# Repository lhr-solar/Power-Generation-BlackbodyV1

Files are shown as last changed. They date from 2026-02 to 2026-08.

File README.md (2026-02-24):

# Power Generation Blackbody
Gathers irradiance and temperature data for telemetry and MPPT algorithmic input.

**Blackbody**

Gathers irradiance reading from sensor board and temperature reading from thermocouple. Sends data on telemetry CAN bus.

**Irradiance Sensor Board**

Holds the irradiance sensor. Placed on the top shell between solar modules and connected with wires to blackbody

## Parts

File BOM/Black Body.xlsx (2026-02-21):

Reference | Qty | Value | DNP | Exclude from BOM | Exclude from Board | Footprint | Datasheet | P/N
Alert_1,Alert_2 | 2 | LED |  |  |  | LED_SMD:LED_0603_1608Metric_Pad1.05x0.95mm_HandSolder | ~ | LS Q976.01-N1Q2-1
C2 | 1 | 1uF |  |  |  | Capacitor_SMD:C_0805_2012Metric_Pad1.18x1.45mm_HandSolder | ~ | MLASU168SB5105KTNA01
C3 | 1 | 0.1u |  |  |  | Capacitor_SMD:C_0805_2012Metric_Pad1.18x1.45mm_HandSolder | ~ | MLASH168SB7104KTNA01
F2 | 1 | 0.5 |  |  |  | Fuse:Fuseholder_Blade_Mini_Keystone_3568 | ~ | 3557-2
FB1,FB2 | 2 | 200 |  |  |  | Inductor_SMD:L_0603_1608Metric_Pad1.05x0.95mm_HandSolder | ~ | 742792910
GND1,Irrad_Fuse1,TP_TC_1,TP_TC_2,TP_TC_F_1,TP_TC_F_2,VCC1 | 7 | TestPoint |  |  |  | TestPoint:TestPoint_Keystone_5005-5009_Compact | ~ | 5015
IC2 | 1 | MCP96L00T-E_MX |  |  |  | BlackBody:QFN65P500X500X100-21N-D | https://datasheet.datasheetarchive.com/originals/distributors/DKDS41/DSANUWW0026539.pdf | MCP96L00T-E/MX
J1 | 1 | 53307-2471 |  |  |  | utsvt_connectors:PeripheralSOM | https://www.molex.com/en-us/products/part-detail-pdf/533072471?display=pdf | 53307-2471
J2 | 1 | Conn_01x02 |  |  |  | utsvt_connectors:105313-2102 | ~ | C17189968
J4 | 1 | LogicAnalyzer |  |  |  | utsvt_connectors:CONN_SFH11-xxxC-D05-ST-XX_SUL | https://www.digikey.com/en/products/detail/sullins-connector-solutions/SFH11-PBPC-D05-ST-BK/1990087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 | SFH11-PBPC-D05-ST-BK
J5 | 1 | Conn_02x04_Top_Bottom |  |  |  | Connector_Molex:Molex_Nano-Fit_105314-xx08_2x04_P2.50mm_Horizontal | ~ | C841208
J7 | 1 | Conn_02x03_Top_Bottom |  |  |  | utsvt_connectors:105314-1306 | ~ | C493437
LOGO1 | 1 | Dr. Hallock |  |  |  | utsvt_logos:LHRs_LOGO
LOGO2 | 1 | Dr. Hallock |  |  |  | utsvt_logos:Hallock_Image_Tiny
R1,R2,R3,R11,R15,R16 | 6 | 10k |  |  |  | Resistor_SMD:R_0603_1608Metric_Pad0.98x0.95mm_HandSolder | ~ | CRCW060310K0FKEI ,CRCW06031K00FKEI ,CRCW080510K0FKEA
R4 | 1 | 1M |  |  |  | Resistor_SMD:R_0603_1608Metric_Pad0.98x0.95mm_HandSolder | ~ | 0603WAF1004T5E
R5,R6 | 2 | 100 |  |  |  | Resistor_SMD:R_0603_1608Metric_Pad0.98x0.95mm_HandSolder | ~ | CRCW0603100RFKEA
R7,R8 | 2 | 2M |  |  |  | Resistor_SMD:R_0603_1608Metric_Pad0.98x0.95mm_HandSolder | ~ | 0603WAF2004T5E
R9 | 1 | 0 |  |  |  | Resistor_SMD:R_0603_1608Metric_Pad0.98x0.95mm_HandSolder | ~ | CRCW06030000Z0EE
R12 | 1 | 43k |  |  |  | Resistor_SMD:R_0603_1608Metric_Pad0.98x0.95mm_HandSolder | ~ | CRCW060343K0FKEI
R13,R14 | 2 | 1k |  |  |  | Resistor_SMD:R_0603_1608Metric_Pad0.98x0.95mm_HandSolder | ~ | CRCW08051K50FKEA

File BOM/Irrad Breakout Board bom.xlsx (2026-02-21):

Quantity | LCSC Part # | "Description" (Customer #)
1 | MLASU168SB5105KTNA01 | Capacitor 0805 1 µF X7R 50 V (Customer: CAP_0805_1uF_X7R)
1 | 105313-1105 | Molex Nano-Fit header, right-angle, 1×5, 2.50 mm (Customer: NANOFIT_RA_1x5)
1 | CRCW080510K0FKEA | Resistor 0805 10 kΩ ±1% (Customer: RES_0805_10K_1PCT)
2 | CRCW08051K50FKEA | Resistor 0805 1.5 kΩ ±1% (Customer: RES_0805_1K5_1PCT)
1 | TSL25911FN | TSL25911FN ambient light sensor, FN package (Customer: TSL25911FN_ALS)

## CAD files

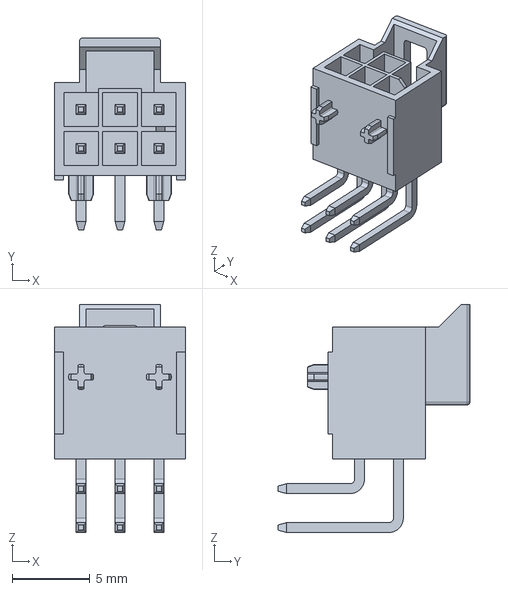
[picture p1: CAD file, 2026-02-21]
Hardware/Blackbody/3D Models/Molex Nanofit 2x3 Connector.stp
8.44 x 12.3 x 14.7 mm

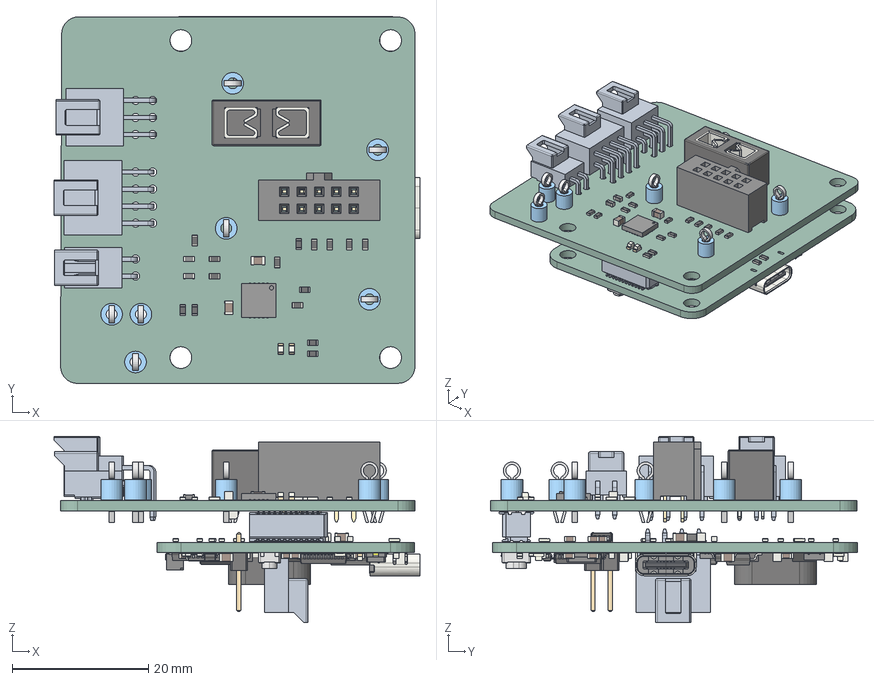
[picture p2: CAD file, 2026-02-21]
Hardware/Blackbody/Black Body.step
53.6 x 53.8 x 27.3 mm
LED_0603_1608Metric x 11
R_0603_1608Metric x 46
ThermalPin x 2
PinsArrayLR x 4
PinsArrayTB x 2
TestPoint_Keystone_5005-5009_Compact x 7
C_0805_2012Metric x 14
SFH11-xC-Dx-ST-BK body_05
pin^SFH11-xC-Dx-ST-BK Ass x 10
L_0603_1608Metric x 2
Fuseholder_Blade_Mini_Keystone_3568
C_0603_1608Metric x 25
D_SOD-123F x 2
LQFP-48_7x7mm_P0.5mm
SOT-223
kicad_embedded_DC8F7DF302591227B9F71E251B6FE682
kicad_embedded_70E7614803E5E4F918B4D78DA69A18BB
L_Coilcraft_MSS1246-XXX
USB_C_Receptacle_GCT_USB4105-xx-A_16P_TopMnt_Horizontal
kicad_embedded_9406EA57197DC5EF7108E35EAA086FA7
BODY-SO x 2
LEAD-D0008A x 8
TL3365AF180QG--3DModel-STEP-520916
BODY-TSSOP
LEAD-TSSOP x 16
PIN1
DAP
SOT-143
D_SOD-123
PinHeader_1x02_P2.54mm_Vertical
D_SOD-323
SOT-23W
LEAD-SO x 8
PeripheralSOM_PCB
Black Body_PCB

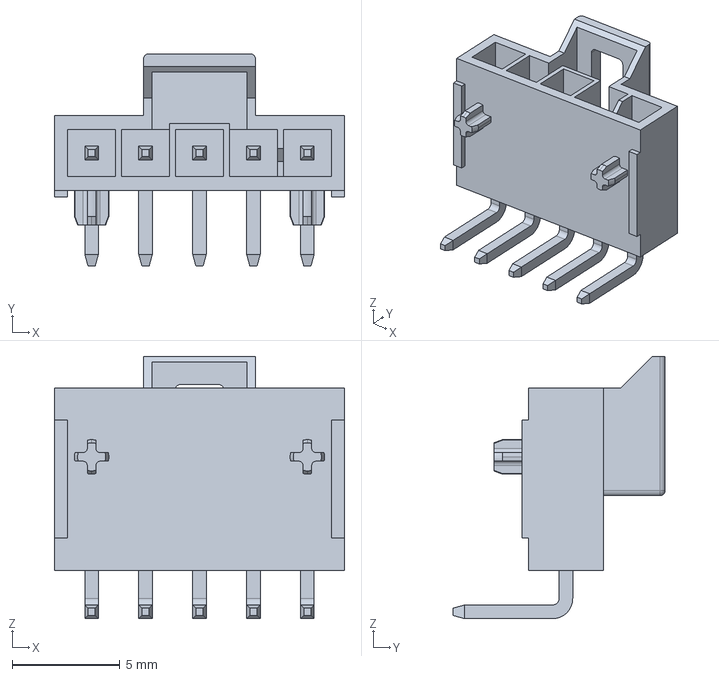
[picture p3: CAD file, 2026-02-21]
Hardware/IrradianceBreakout/3D Models/Molex Nanofit 1x5 Connector.stp
13.4 x 9.84 x 12.2 mm

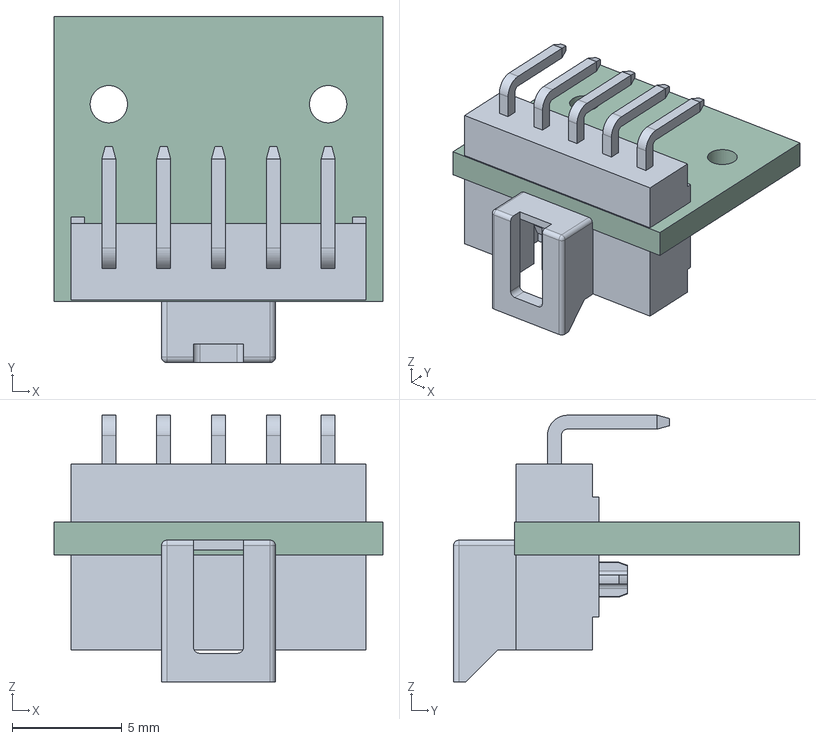
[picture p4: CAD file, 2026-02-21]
Hardware/IrradianceBreakout/Black Body Breakout Board.step
15.0 x 15.8 x 12.2 mm
Black Body Breakout Board_PCB

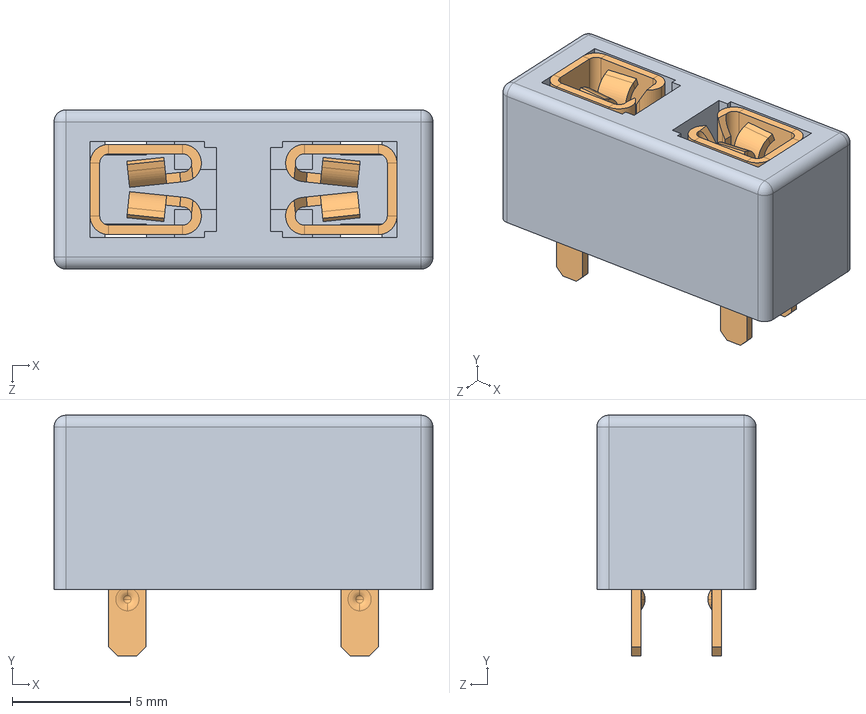
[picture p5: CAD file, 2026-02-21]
Hardware/Blackbody/3D Models/Fuse 3658.STEP
16.0 x 10.2 x 6.73 mm
F3568-1
3557_rev.C x 2

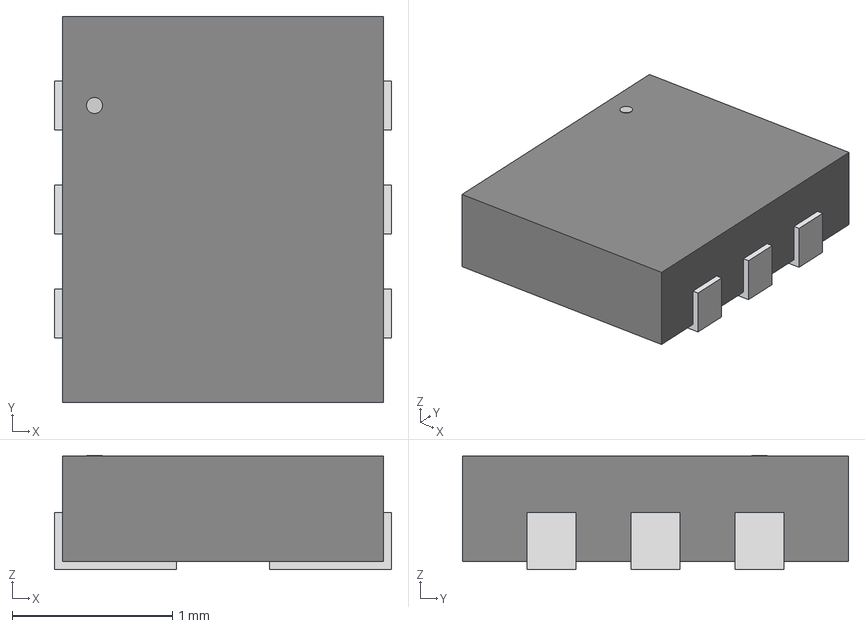
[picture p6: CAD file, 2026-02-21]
Hardware/IrradianceBreakout/3D Models/Irrad IC.step
2.11 x 2.41 x 0.714 mm

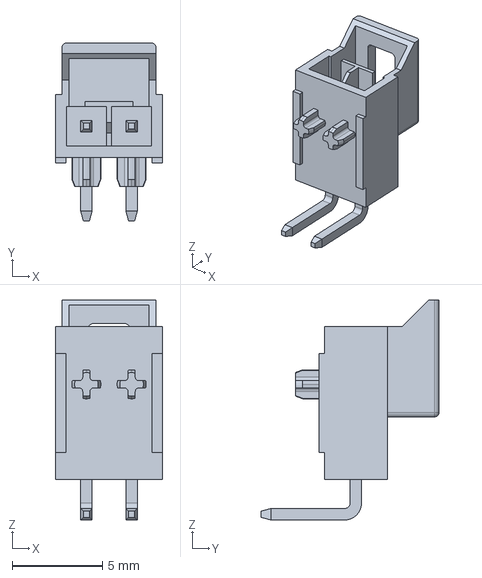
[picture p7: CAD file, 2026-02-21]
Hardware/Blackbody/3D Models/Molex Nanofit 1x2 Connector.stp
5.94 x 9.84 x 12.2 mm

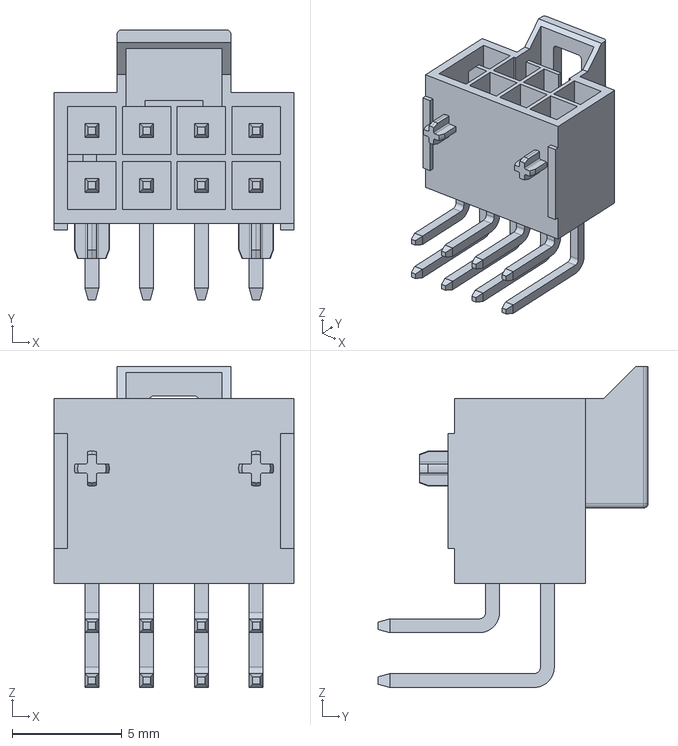
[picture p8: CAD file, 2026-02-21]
Hardware/Blackbody/3D Models/Molex Nanofit 2x4 Connector.stp
10.9 x 12.3 x 14.7 mm

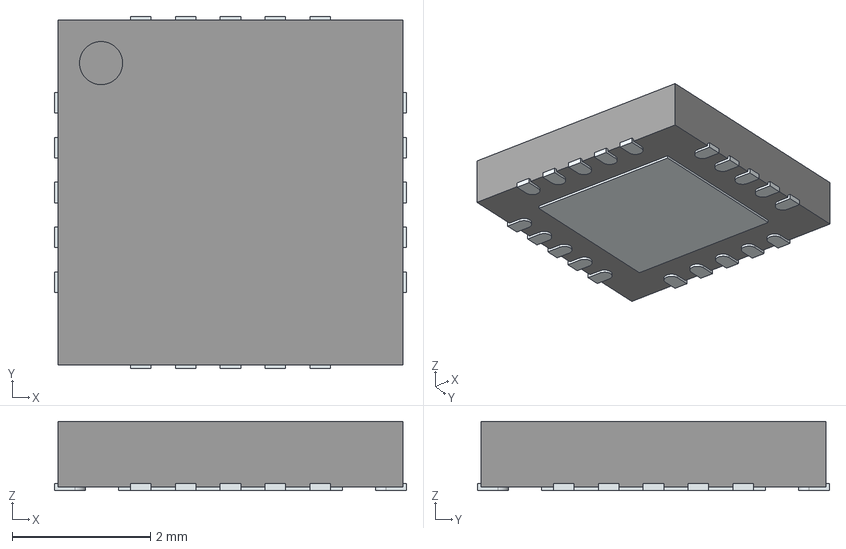
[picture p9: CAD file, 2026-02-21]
Hardware/Blackbody/3D Models/MCP96L00T-E_MX.stp
5.10 x 5.10 x 1.00 mm
ThermalPin
PinsArrayLR
PinsArrayTB

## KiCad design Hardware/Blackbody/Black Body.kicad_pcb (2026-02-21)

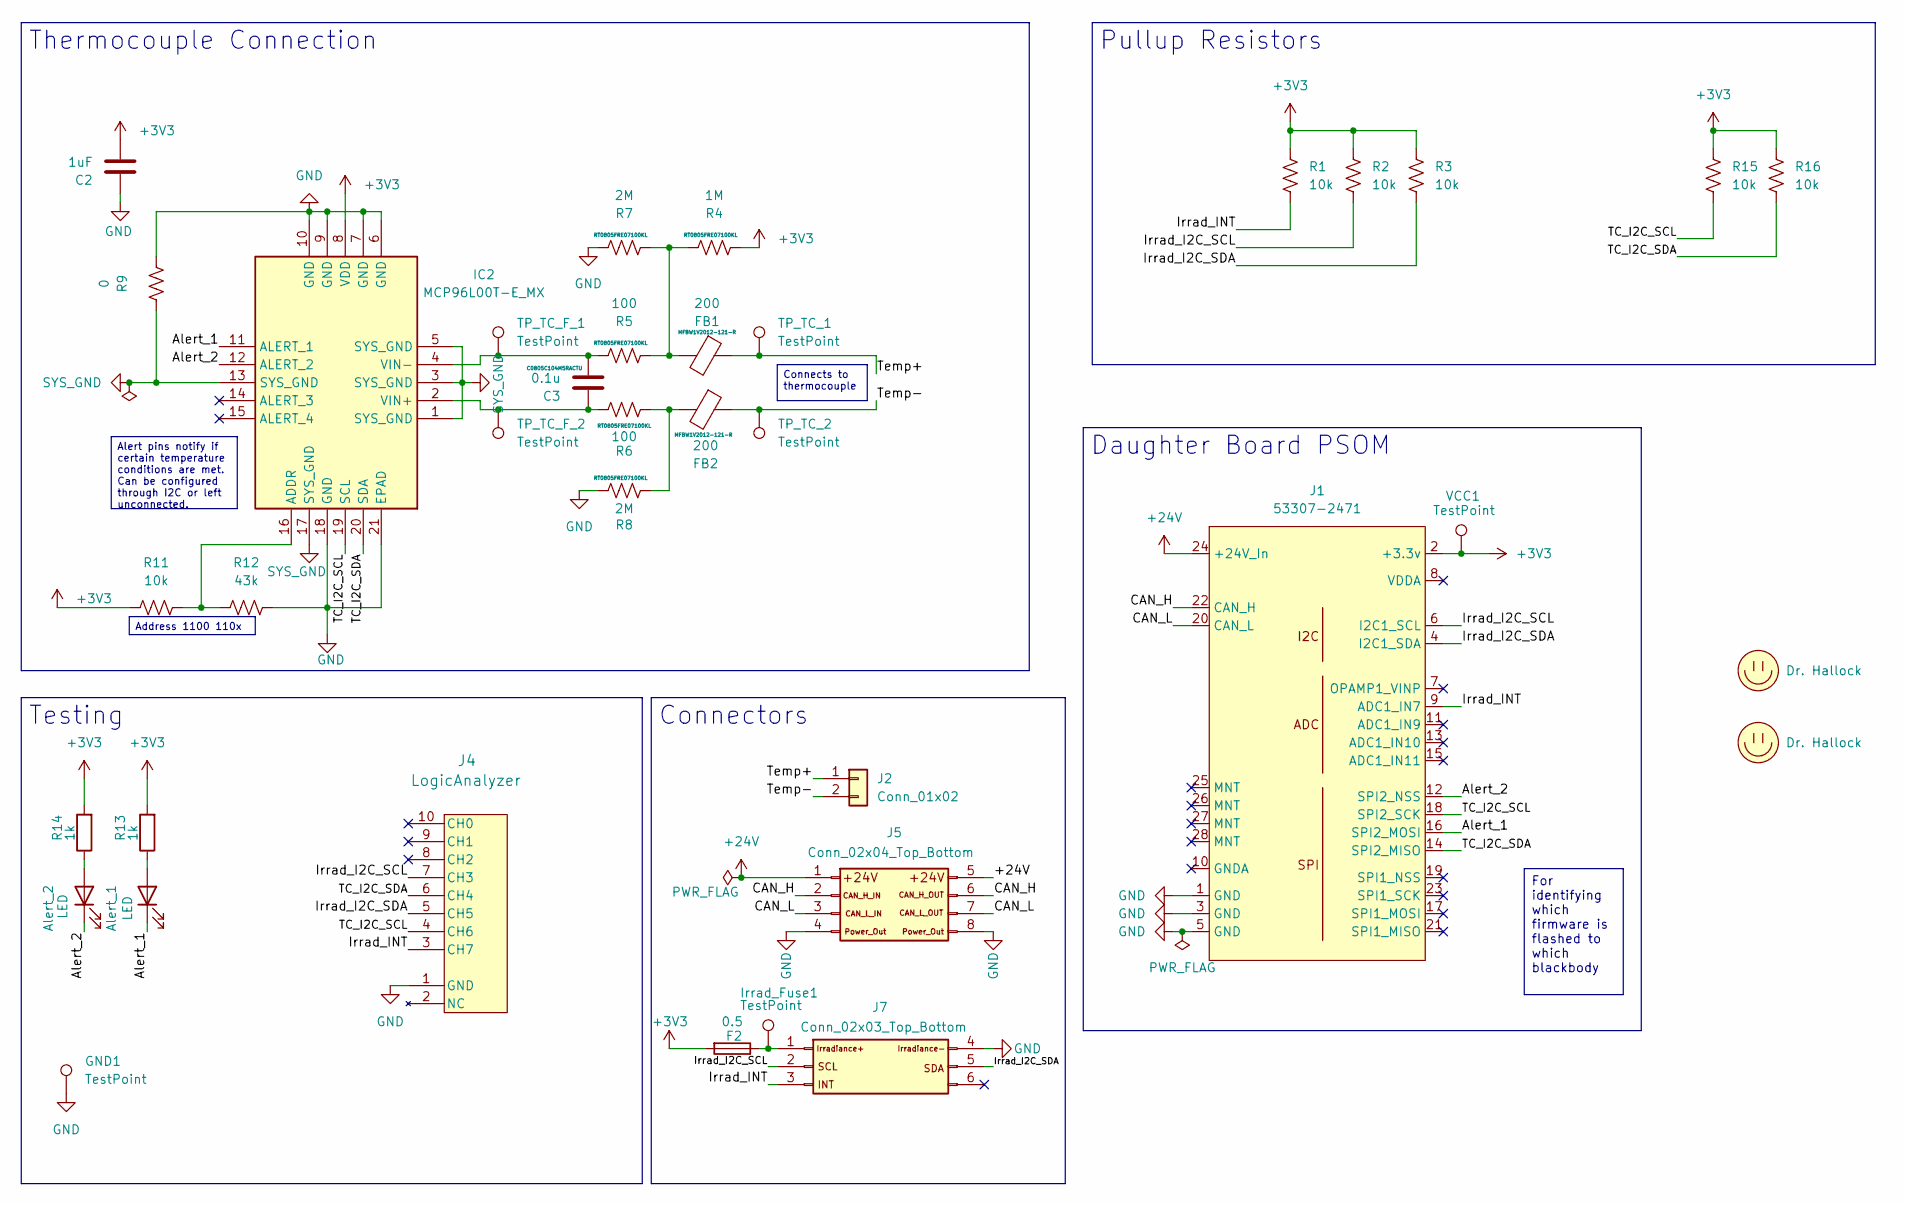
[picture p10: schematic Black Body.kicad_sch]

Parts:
Alert_1, Alert_2: LED; LED_0603_1608Metric_Pad1.05x0.95mm_HandSolder
C2: 1uF; C_0603_1608Metric_Pad1.08x0.95mm_HandSolder
C3: 0.1u; C_0603_1608Metric_Pad1.08x0.95mm_HandSolder
F2: 0.5; Fuseholder_Blade_Mini_Keystone_3568
FB1, FB2: 200; L_0603_1608Metric_Pad1.05x0.95mm_HandSolder
GND1: TestPoint; TestPoint_Keystone_5005-5009_Compact
IC2: MCP96L00T-E_MX; QFN65P500X500X100-21N-D; Manufacturer_Part_Number MCP96L00T-E/MX; Mouser Part Number 579-MCP96L00T-E/MX
Irrad_Fuse1: TestPoint; TestPoint_Keystone_5005-5009_Compact
J1: 53307-2471; PeripheralSOM
J2: Conn_01x02; 105313-2102
J4: LogicAnalyzer; CONN_SFH11-xxxC-D05-ST-XX_SUL; Digikey P/N S9194-ND
J5: Conn_02x04_Top_Bottom; Molex_Nano-Fit_105314-xx08_2x04_P2.50mm_Horizontal
J7: Conn_02x03_Top_Bottom; 105314-1306
LOGO1: Dr. Hallock; LHRs_LOGO
LOGO2: Dr. Hallock; Hallock_Image_Tiny
R1, R2, R3, R11, R15, R16: 10k; R_0603_1608Metric_Pad0.98x0.95mm_HandSolder
R4: 1M; R_0603_1608Metric_Pad0.98x0.95mm_HandSolder
R5, R6: 100; R_0603_1608Metric_Pad0.98x0.95mm_HandSolder
R7, R8: 2M; R_0603_1608Metric_Pad0.98x0.95mm_HandSolder
R9: 0; R_0603_1608Metric_Pad0.98x0.95mm_HandSolder
R12: 43k; R_0603_1608Metric_Pad0.98x0.95mm_HandSolder
R13, R14: 1k; R_0603_1608Metric_Pad0.98x0.95mm_HandSolder
TP_TC_1, TP_TC_2: TestPoint; TestPoint_Keystone_5005-5009_Compact
TP_TC_F_1, TP_TC_F_2: TestPoint; TestPoint_Keystone_5005-5009_Compact
VCC1: TestPoint; TestPoint_Keystone_5005-5009_Compact

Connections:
+3V3: C2.2, F2.2, IC2.8 (VDD), J1.2 (+3.3v), R1.1, R2.1, R3.1, R4.2, R11.2, R13.2, R14.2, R15.1, R16.1, VCC1.1
+24V: J1.24 (+24V_In), J5.1, J5.5
/Alert_1: Alert_1.1 (K), IC2.11 (ALERT_1), J1.16 (SPI2_MOSI)
/Alert_2: Alert_2.1 (K), IC2.12 (ALERT_2), J1.12 (SPI2_NSS)
/CAN_H: J1.22 (CAN_H), J5.2, J5.6
/CAN_L: J1.20 (CAN_L), J5.3, J5.7
/Irrad_I2C_SCL: J1.6 (I2C1_SCL), J4.7 (CH3), J7.2, R2.2
/Irrad_I2C_SDA: J1.4 (I2C1_SDA), J4.5 (CH5), J7.5, R3.2
/Irrad_INT: J1.9 (ADC1_IN7), J4.3 (CH7), J7.3, R1.2
/TC_I2C_SCL: IC2.19 (SCL), J1.18 (SPI2_SCK), J4.4 (CH6), R15.2
/TC_I2C_SDA: IC2.20 (SDA), J1.14 (SPI2_MISO), J4.6 (CH4), R16.2
/Temp+: FB1.1, J2.1, TP_TC_1.1
/Temp-: FB2.1, J2.2, TP_TC_2.1
GND: C2.1, GND1.1, IC2.6 (GND), IC2.7 (GND), IC2.9 (GND), IC2.10 (GND), IC2.18 (GND), IC2.21 (EPAD), J1.1 (GND), J1.3 (GND), J1.5 (GND), J4.1 (GND), J5.4, J5.8, J7.4, R7.1, R8.1, R9.2, R12.1
unnamed: Alert_1.2 (A), R13.1
unnamed: Alert_2.2 (A), R14.1
unnamed: FB1.2, R4.1, R5.2, R7.2
unnamed: FB2.2, R6.2, R8.2
unnamed: IC2.16 (ADDR), R11.1, R12.2
unnamed: C3.1, IC2.2 (VIN+), R6.1, TP_TC_F_2.1
unnamed: C3.2, IC2.4 (VIN-), R5.1, TP_TC_F_1.1
unnamed: F2.1, Irrad_Fuse1.1, J7.1
SYS_GND: IC2.1 (SYS_GND), IC2.3 (SYS_GND), IC2.5 (SYS_GND), IC2.13 (SYS_GND), IC2.17 (SYS_GND), R9.1

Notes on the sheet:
Connects to thermocouple
Daughter Board PSOM
Pullup Resistors
Address 1100 110x
For identifying which firmware is flashed to which blackbody
Thermocouple Connection
Testing
Alert pins notify if certain temperature conditions are met. Can be configured through I2C or left unconnected.
Connectors

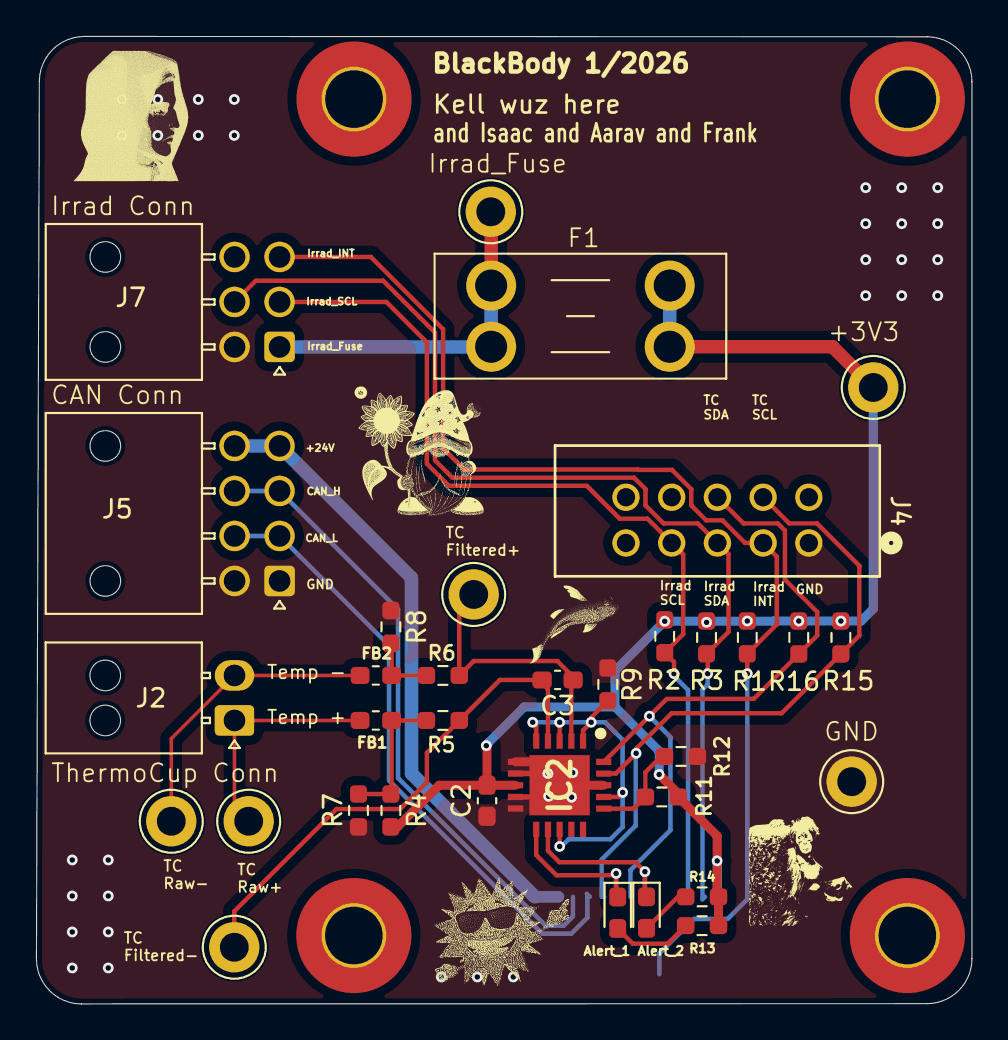
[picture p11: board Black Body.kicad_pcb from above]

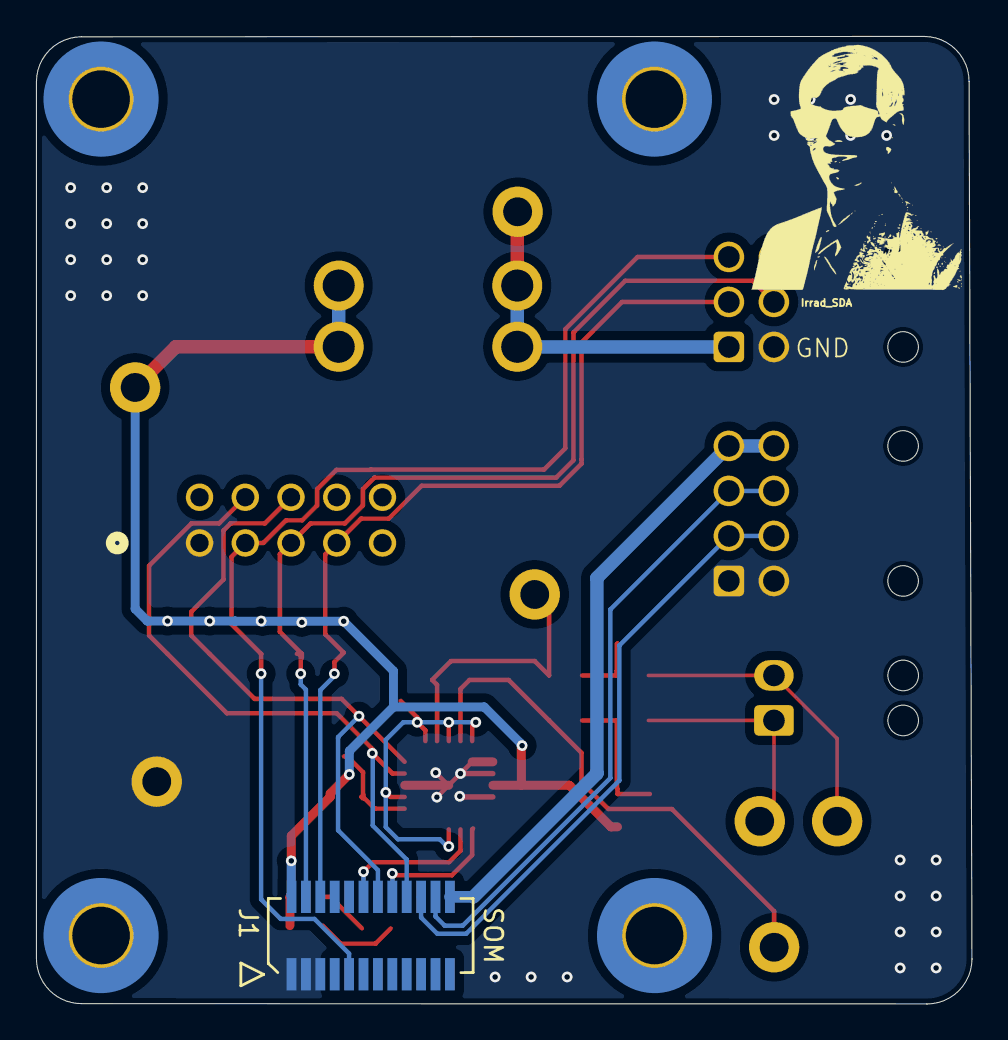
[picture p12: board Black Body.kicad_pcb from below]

Board: 2 copper layers, 52.0 x 53.8 mm, 37 parts (2 on the bottom side), 23 nets.

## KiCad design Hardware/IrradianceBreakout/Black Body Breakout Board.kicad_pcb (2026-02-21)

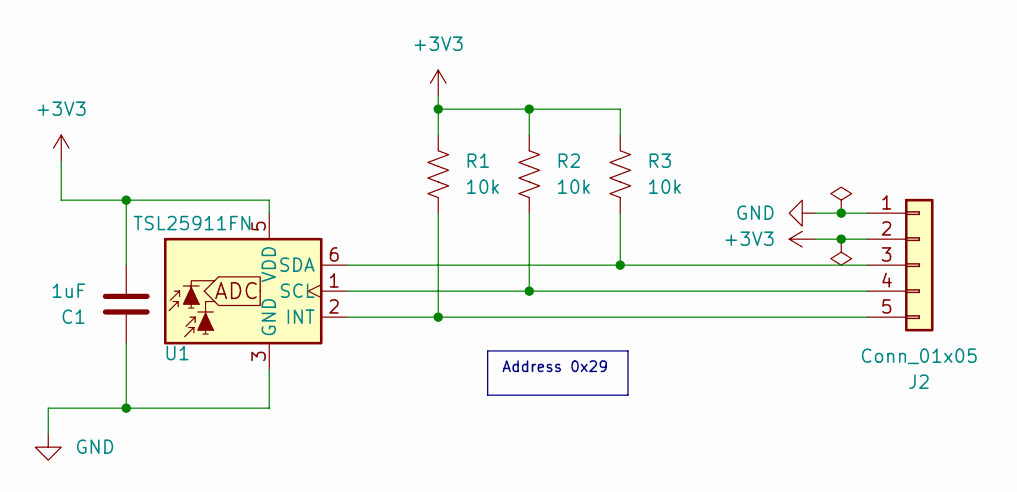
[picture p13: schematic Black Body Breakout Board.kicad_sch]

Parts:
C1: 1uF; C_0603_1608Metric_Pad1.08x0.95mm_HandSolder
J2: Conn_01x05; Molex_Nano-Fit_105313-xx05_1x05_P2.50mm_Horizontal
R1, R2, R3: 10k; R_0603_1608Metric_Pad0.98x0.95mm_HandSolder
U1: TSL25911FN; AMS_TSL25911FN

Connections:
+3V3: C1.2, J2.2, R1.1, R2.1, R3.1, U1.5 (VDD)
GND: C1.1, J2.1, U1.3 (GND)
unnamed: J2.3, R3.2, U1.6 (SDA)
unnamed: J2.4, R2.2, U1.1 (SCL)
unnamed: J2.5, R1.2, U1.2 (INT)

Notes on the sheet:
Address 0x29

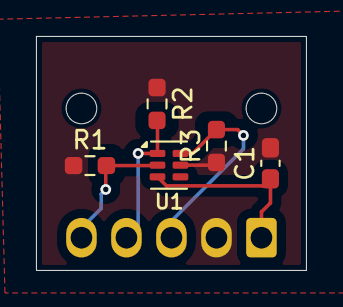
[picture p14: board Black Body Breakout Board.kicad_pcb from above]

Board: 2 copper layers, 15.0 x 13.0 mm, 6 parts (1 on the bottom side), 5 nets.

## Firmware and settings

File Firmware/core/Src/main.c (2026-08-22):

#include "stm32xx_hal.h"
#include "irrad.h"
#include "thermo.h"
#include "FreeRTOS.h"
#include "task.h"
#include "pinDefs.h"
#include "projdefs.h"
#include "printf.h"
#include "UART.h"
#include "CAN.h"

#define QUEUE_LENGTH 50

#define ARRAY_FRONT_RIGHT_ID 0x600
#define ARRAY_FRONT_LEFT_ID 0x620
#define ARRAY_MIDDLE_RIGHT_ID 0x630
#define ARRAY_MIDDLE_LEFT_ID 0x650
#define ARRAY_BACK_RIGHT_ID 0x660
#define ARRAY_BACK_LEFT_ID 0x680

StaticTask_t heartbeatTaskTCB;
StackType_t heartbeatTaskStack[256];

StaticTask_t irradTaskTCB;
StackType_t irradTaskStack[1024];

StaticTask_t thermoTaskTCB;
StackType_t thermoTaskStack[1024];

StaticTask_t CANTaskTCB;
StackType_t CANTaskStack[1024];

static QueueHandle_t IrradQueue;
static StaticQueue_t IrradQueueBuffer;
static uint32_t IrradQueueStorage[QUEUE_LENGTH];

static QueueHandle_t ThermoQueue;
static StaticQueue_t ThermoQueueBuffer;
static uint32_t ThermoQueueStorage[QUEUE_LENGTH];

TSL25911FN_HandleTypeDef irrad_handle;
MCP9600_HandleTypeDef thermo_handle;

I2C_HandleTypeDef hi2c1;
I2C_HandleTypeDef hi2c2;


void HeartbeatTask(void *argument)
{
    __HAL_RCC_GPIOB_CLK_ENABLE();
    GPIO_InitTypeDef led_config = {0};
    led_config.Mode = GPIO_MODE_OUTPUT_PP;
    led_config.Pull = GPIO_NOPULL;
    led_config.Pin = PSOM_HEARTBEAT_LED_PIN;
    led_config.Speed = GPIO_SPEED_FREQ_LOW;
    HAL_GPIO_Init(PSOM_HEARTBEAT_LED_PORT, &led_config);
    HAL_GPIO_WritePin(PSOM_HEARTBEAT_LED_PORT, PSOM_HEARTBEAT_LED_PIN, GPIO_PIN_SET);

    (void)argument;

    while (1)
    {
      HAL_GPIO_TogglePin(PSOM_HEARTBEAT_LED_PORT, PSOM_HEARTBEAT_LED_PIN);
      vTaskDelay(pdMS_TO_TICKS(500));
    }

}

void IrradTask(void *argument){
    tsl25911fn_status_t irrad_status;
    TSL25911FN_data_t irrad_data = {0};

    uint32_t white_int;
    uint32_t white_frac;
    uint32_t infrared_int;
    uint32_t infrared_frac;


    irrad_status = tsl25911fn_init(&irrad_handle, &hi2c1);

    if(irrad_status != TSL25911FN_WRITE_FAIL){
        printf("status %d \n\r" , irrad_status);
    }


    irrad_status = tsl25911fn_power_on(&irrad_handle, 
                                pdMS_TO_TICKS(10));

    irrad_status = tsl25911fn_set_control(&irrad_handle,
                                            irrad_handle.control,
                                            pdMS_TO_TICKS(10));

    UNUSED(irrad_status);

    while (1){

        irrad_status = tsl25911fn_read_data(&irrad_handle,
                                            &irrad_data,
                                            pdMS_TO_TICKS(10)); 

        if (irrad_status == TSL25911FN_OK)
        {
            white_int =(uint32_t)(irrad_data.irrad_whitelight_q16 >> 16);

            white_frac = (uint32_t)(((irrad_data.irrad_whitelight_q16 & 0xFFFFULL) * 10000ULL) >> 16);

            infrared_int = (uint32_t)(irrad_data.irrad_infrared_q16 >> 16);

            infrared_frac = (uint32_t)(((irrad_data.irrad_infrared_q16 & 0xFFFFULL) * 10000ULL) >> 16);

            if (irrad_data.ch0 >= 36000 || irrad_data.ch1 >= 36000)
                {
                    printf("Sensor saturated\r\n");
                }

            printf("CH0: %u CH1: %u\r\n",
                   irrad_data.ch0,
                   irrad_data.ch1);

            printf("White Light Irradiance: %lu.%04lu\r\n",
                   white_int,
                   white_frac);

            printf("Infrared Light Irradiance: %lu.%04lu\r\n",
                   infrared_int,
                   infrared_frac);
        }
        else
        {
            printf("Irradiance read failed\r\n");
        }

        uint32_t irrad_packed = ((uint16_t)irrad_data.ch1 << 16) | (uint16_t)irrad_data.ch0;

        if (uxQueueSpacesAvailable(IrradQueue) > 0){
            xQueueSend(
            IrradQueue,
            &irrad_packed,
            200);
        }
        printf("Irrad Packed %ld\r\n", irrad_packed);

        //integration time for the sensor is 100ms on max gain
        vTaskDelay(pdMS_TO_TICKS(200)); 
        
    }
}


void ThermoTask(void *argument){
    mcp9600_status_t thermo_status;
    thermo_status = mcp9600_init(&thermo_handle,
                                &hi2c2,
                                MCP9600_7BIT_ADDR_6);
    UNUSED(thermo_status);
                    
    int32_t temp_int = 0;
    int32_t temp_frac = 0;
    uint16_t raw_temperature = 0;

        while (1){
            thermo_status = mcp9600_read_hot_junction(&thermo_handle,
                                            &temp_int,
                                            &temp_frac,
                                            &raw_temperature,
                                            pdMS_TO_TICKS(100));
            
            printf("Temperature: %ld.%04ld C\r\n", temp_int, temp_frac);
            //maybe 80ms for reading idfk thou just a guess

        uint16_t thermo_packed = raw_temperature;

        if (uxQueueSpacesAvailable(ThermoQueue) > 0){
            xQueueSend(
            ThermoQueue,
            &thermo_packed,
            200);
        }
        printf("Thermo Packed %d\r\n", thermo_packed);

            vTaskDelay(pdMS_TO_TICKS(200));
        }
}

void CANTask(void *argument){

        uint32_t irrad_recieved;
        uint16_t thermo_recieved;
        CAN_TxHeaderTypeDef tx_header = {0};   
        tx_header.StdId = ARRAY_MIDDLE_RIGHT_ID; //EDIT THIS FOR EACH BB
        tx_header.RTR = CAN_RTR_DATA;
        tx_header.IDE = CAN_ID_STD;
        tx_header.DLC = 6;
        tx_header.TransmitGlobalTime = DISABLE;

        uint8_t tx_data[8] = {0};
        //White Light Irrad
        tx_data[0] = 0x00;
        tx_data[1] = 0x00;

        //Infared Irrad
        tx_data[2] = 0x00;
        tx_data[3] = 0x00;

        //Thermo Temp
        tx_data[4] = 0x00;
        tx_data[5] = 0x00;

        while (1){
        
            if (uxQueueMessagesWaiting(IrradQueue) != 0){
                if (xQueueReceive(
                        IrradQueue,
                        &irrad_recieved,
                        200) == pdPASS)
                {

                    printf("Irrad recieved %ld\r\n" , irrad_recieved);
                    tx_data[0] = irrad_recieved & 0x000000FF;
                    tx_data[1] = (irrad_recieved & 0x0000FF00) >> 8;
                    tx_data[2] = (irrad_recieved & 0x00FF0000) >> 16;
                    tx_data[3] = (irrad_recieved & 0xFF000000) >> 24;
                    
                }
            }

            if (uxQueueMessagesWaiting(ThermoQueue) != 0){
                if (xQueueReceive(
                        ThermoQueue,
                        &thermo_recieved,
                        200) == pdPASS)
                {
                    
                    printf("Thermo recieved %d\r\n", thermo_recieved);
                    tx_data[4] = thermo_recieved & 0x00FF;
                    tx_data[5] = (thermo_recieved & 0xFF00) >> 8;
                }

            }

            if (can_send(hcan1, &tx_header, tx_data, 200) != CAN_OK){

                printf("can okay %ld\n\r", hcan1->ErrorCode);
                HAL_GPIO_WritePin(PSOM_LED3_PORT, PSOM_LED3_PIN, GPIO_PIN_SET);
        }
            //matched both tasks for data collection
            vTaskDelay(pdMS_TO_TICKS(200));
        }
}

void printfstart(void){
    husart1->Instance = USART1;
    husart1->Init.BaudRate = 115200;
    husart1->Init.WordLength = UART_WORDLENGTH_8B;
    husart1->Init.StopBits = UART_STOPBITS_1;
    husart1->Init.Parity = UART_PARITY_NONE;
    husart1->Init.Mode = UART_MODE_TX_RX;
    husart1->Init.HwFlowCtl = UART_HWCONTROL_NONE;
    husart1->Init.OverSampling = UART_OVERSAMPLING_16;

    printf_init(husart1);
        
}

void canstart(void){
 hcan1->Instance = CAN1;
// create filter
  CAN_FilterTypeDef  sFilterConfig;
  sFilterConfig.FilterBank = 0;
  sFilterConfig.FilterMode = CAN_FILTERMODE_IDMASK;
  sFilterConfig.FilterScale = CAN_FILTERSCALE_32BIT;
  sFilterConfig.FilterIdHigh = 0x0000;
  sFilterConfig.FilterIdLow = 0x0000;
  sFilterConfig.FilterMaskIdHigh = 0x0000;
  sFilterConfig.FilterMaskIdLow = 0x0000;
  sFilterConfig.FilterFIFOAssignment = CAN_RX_FIFO0;
  sFilterConfig.FilterActivation = ENABLE;
  sFilterConfig.SlaveStartFilterBank = 14;

  // setup can1 init
  // Baud rate is 250 kbit/s
  hcan1->Init.Prescaler = 20;
  hcan1->Init.SyncJumpWidth = CAN_SJW_1TQ;
  hcan1->Init.TimeSeg1 = CAN_BS1_13TQ;
  hcan1->Init.TimeSeg2 = CAN_BS2_2TQ;
  hcan1->Init.Mode = CAN_MODE_NORMAL;
  hcan1->Init.TimeTriggeredMode = DISABLE;
  hcan1->Init.AutoBusOff = ENABLE;
  hcan1->Init.AutoWakeUp = DISABLE;
  hcan1->Init.AutoRetransmission = ENABLE;
  hcan1->Init.ReceiveFifoLocked = DISABLE;

  // If TransmitFifoPriority is disabled, the hardware selects the mailbox based on the message ID priority. 
  // If enabled, the hardware uses a FIFO mechanism to select the mailbox based on the order of transmission requests.
  hcan1->Init.TransmitFifoPriority = ENABLE;

  // initialize CAN1
  if (can_init(hcan1, &sFilterConfig) != CAN_OK) Error_Handler();
  if (can_start(hcan1) != CAN_OK) Error_Handler();
}


int main() {
    HAL_Init();
    SystemClock_Config();

    __HAL_RCC_GPIOB_CLK_ENABLE();
    GPIO_InitTypeDef led_config = {0};
    led_config.Mode = GPIO_MODE_OUTPUT_PP;
    led_config.Pull = GPIO_NOPULL;
    led_config.Pin = PSOM_HEARTBEAT_LED_PIN;
    led_config.Speed = GPIO_SPEED_FREQ_LOW;
    HAL_GPIO_Init(PSOM_HEARTBEAT_LED_PORT, &led_config);

    __HAL_RCC_GPIOA_CLK_ENABLE();
    led_config.Mode = GPIO_MODE_OUTPUT_PP;
    led_config.Pull = GPIO_NOPULL;
    led_config.Pin = PSOM_LED3_PIN;
    led_config.Speed = GPIO_SPEED_FREQ_LOW;
    HAL_GPIO_Init(PSOM_LED3_PORT, &led_config);



    printfstart();
    
    canstart();



    IrradQueue = xQueueCreateStatic(
        QUEUE_LENGTH,
        sizeof(uint32_t),
        (uint8_t *)IrradQueueStorage,
        &IrradQueueBuffer
    );

    ThermoQueue = xQueueCreateStatic(
        QUEUE_LENGTH,
        sizeof(uint16_t),
        (uint8_t *)ThermoQueueStorage,
        &ThermoQueueBuffer
    );

    xTaskCreateStatic(HeartbeatTask,
                        "Heartbeat",
                        256,
                        NULL,
                        tskIDLE_PRIORITY + 1,
                        heartbeatTaskStack,
                        &heartbeatTaskTCB);

    xTaskCreateStatic(IrradTask,
                        "Irrad",
                        1024,
                        NULL,
                        tskIDLE_PRIORITY + 2,
                        irradTaskStack,
                        &irradTaskTCB);

    xTaskCreateStatic(ThermoTask,
                        "Thermo",
                        1024,
                        NULL,
                        tskIDLE_PRIORITY + 2,
                        thermoTaskStack,
                        &thermoTaskTCB);

    xTaskCreateStatic(CANTask,
                        "CAN",
                        1024,
                        NULL,
                        tskIDLE_PRIORITY + 3,
                        CANTaskStack,
                        &CANTaskTCB);

    vTaskStartScheduler();

    while (1){}

}


void HAL_I2C_MspInit(I2C_HandleTypeDef* hi2c)
{
  GPIO_InitTypeDef GPIO_InitStruct = {0};
  RCC_PeriphCLKInitTypeDef PeriphClkInit = {0};
  if(hi2c->Instance==I2C1)
  {
    PeriphClkInit.PeriphClockSelection = RCC_PERIPHCLK_I2C1;
    PeriphClkInit.I2c1ClockSelection = RCC_I2C1CLKSOURCE_PCLK1;
    if (HAL_RCCEx_PeriphCLKConfig(&PeriphClkInit) != HAL_OK)
    {
      Error_Handler();
    }
    __HAL_RCC_GPIOB_CLK_ENABLE();

    /**I2C1 GPIO Configuration
    PB6     ------> I2C1_SCL
    PB7     ------> I2C1_SDA
    */
    GPIO_InitStruct.Pin = GPIO_PIN_6|GPIO_PIN_7;
    GPIO_InitStruct.Mode = GPIO_MODE_AF_OD;
    GPIO_InitStruct.Pull = GPIO_NOPULL;
    GPIO_InitStruct.Speed = GPIO_SPEED_FREQ_VERY_HIGH;
    GPIO_InitStruct.Alternate = GPIO_AF4_I2C1;
    HAL_GPIO_Init(GPIOB, &GPIO_InitStruct);

    /* Peripheral clock enable */
    __HAL_RCC_I2C1_CLK_ENABLE();
  }

    //MSP Init for Thermo Code
    GPIO_InitTypeDef GPIO_InitStruct2 = {0};
    RCC_PeriphCLKInitTypeDef PeriphClkInit2 = {0};
    if(hi2c->Instance==I2C2)
    {
        PeriphClkInit2.PeriphClockSelection = RCC_PERIPHCLK_I2C2;
        PeriphClkInit2.I2c2ClockSelection = RCC_I2C2CLKSOURCE_PCLK1;
        if (HAL_RCCEx_PeriphCLKConfig(&PeriphClkInit2) != HAL_OK)
        {
        Error_Handler();
        }

        __HAL_RCC_GPIOB_CLK_ENABLE();

        GPIO_InitStruct2.Pin = GPIO_PIN_10|GPIO_PIN_14;
        GPIO_InitStruct2.Mode = GPIO_MODE_AF_OD;
        GPIO_InitStruct2.Pull = GPIO_NOPULL;
        GPIO_InitStruct2.Speed = GPIO_SPEED_FREQ_VERY_HIGH;
        GPIO_InitStruct2.Alternate = GPIO_AF4_I2C2;
        HAL_GPIO_Init(GPIOB, &GPIO_InitStruct2);

        __HAL_RCC_I2C2_CLK_ENABLE();
    }

}

void HAL_CAN_MspInit(CAN_HandleTypeDef* hcan) {
  GPIO_InitTypeDef GPIO_InitStruct = {0};
  if(hcan->Instance==CAN1) {
    /* Peripheral clock enable */
    __HAL_RCC_CAN1_CLK_ENABLE();

    __HAL_RCC_GPIOB_CLK_ENABLE();
    /**CAN1 GPIO Configuration
    PB8     ------> CAN1_RX
    PB9     ------> CAN1_TX
    */
    GPIO_InitStruct.Pin = GPIO_PIN_8|GPIO_PIN_9;
    GPIO_InitStruct.Mode = GPIO_MODE_AF_PP;
    GPIO_InitStruct.Pull = GPIO_NOPULL;
    GPIO_InitStruct.Speed = GPIO_SPEED_FREQ_VERY_HIGH;
    GPIO_InitStruct.Alternate = GPIO_AF9_CAN1;
    HAL_GPIO_Init(GPIOB, &GPIO_InitStruct);

    /* CAN1 interrupt Init */
    HAL_NVIC_SetPriority(CAN1_TX_IRQn, configLIBRARY_MAX_SYSCALL_INTERRUPT_PRIORITY, 0);
    HAL_NVIC_EnableIRQ(CAN1_TX_IRQn);
    HAL_NVIC_SetPriority(CAN1_RX0_IRQn, configLIBRARY_MAX_SYSCALL_INTERRUPT_PRIORITY, 0);
    HAL_NVIC_EnableIRQ(CAN1_RX0_IRQn);
  }
}

void HAL_CAN_MspDeInit(CAN_HandleTypeDef* hcan) {
  if(hcan->Instance==CAN1) {
    /* Peripheral clock disable */
    __HAL_RCC_CAN1_CLK_DISABLE();

    /**CAN1 GPIO Configuration
    PB8     ------> CAN1_RX
    PB9     ------> CAN1_TX
    */
    HAL_GPIO_DeInit(GPIOB, GPIO_PIN_8|GPIO_PIN_9);

    /* CAN1 interrupt DeInit */
    HAL_NVIC_DisableIRQ(CAN1_TX_IRQn);
    HAL_NVIC_DisableIRQ(CAN1_RX0_IRQn);
  }
}

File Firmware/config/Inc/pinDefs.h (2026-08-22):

/* Define GPIO pins and functions */

#define PSOM_HEARTBEAT_LED_PORT GPIOB
#define PSOM_HEARTBEAT_LED_PIN GPIO_PIN_11

#define PSOM_LED3_PORT GPIOA
#define PSOM_LED3_PIN GPIO_PIN_8

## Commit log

2024-11-17 sensor board
    [NTCLE203E3103GB0.stp, sensor_board.kicad_pcb, sensor_board.kicad_sch]
2024-12-07 added more complexity + thermistor connection
    [RTD.kicad_sch, blackbody_a.kicad_sch, blackbody_c.kicad_sch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]
2025-01-25 Initial version of sensor communication through all three boards
    [blackbody_c.kicad_sch, irradiance.kicad_sch, sensing.kicad_sch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]
2025-01-25 Updated minor errors
    [blackbody_c.kicad_sch, irradiance.kicad_sch, sensing.kicad_sch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]
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2025-02-08 Added controller and CAN
    [blackbody_a.kicad_sch, can_comm.kicad_sch, controller.kicad_sch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]
2025-02-22 Added power distribution
    [LM76202QPWPRQ1.stp, TPS562231DRLR.stp, blackbody_a.kicad_sch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]
2025-02-25 minor errors
    [blackbody_a.kicad_sch, controller.kicad_sch, power_dist.kicad_sch]
2025-03-12 Fixed pins, minor changes, removed power isolation
    [TCAN337DCNR.step, blackbody_a.kicad_sch, blackbody_c.kicad_sch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]
2025-03-12 add testpoints
    [blackbody_c.kicad_sch, irradiance.kicad_sch, temperature.kicad_sch]
2025-03-12 review changes
    [blackbody_a.kicad_sch, can_comm.kicad_sch]
2025-04-09 layout iteration 1
    [1053091104.step, 1053101104.stp, blackbody_a.kicad_pcb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]
2025-04-24 layout edits
    [01x02nanofit.stp, 1054291204.stp, blackbody_a.kicad_pcb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]
2025-05-05 layout updates
    [105313-1202.stp, 1053131104.stp, 105405-1104.stp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]
2025-05-10 fixed footprint issue
    [105309-1102.stp, 43650-0215.stp, B3SL-1002P.stp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]
2025-09-26 Cleaned repo. Added new blackbody A kicad project
    [01x02nanofit.stp, 105309-1102.stp, 1053091104.step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]
2025-10-04 Layout Added
    [75757-4160.SchLib, 75757-4160.stp, 757574160.PcbLib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]
2025-10-04 adding readme
    [75757-4160.SchLib, 75757-4160.stp, 757574160.PcbLib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]
2025-10-04 adding gitignore
    [75757-4160.SchLib, 75757-4160.stp, 757574160.PcbLib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]
2025-10-04 cleaned up files
    [75757-4160.SchLib, 75757-4160.stp, 757574160.PcbLib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]
2025-10-04 Added irradiance breakout
    [Black Body Breakout Board.kicad_pcb, Black Body Breakout Board.kicad_sch, Black Body.kicad_pcb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]
2025-10-11 Updated Layout
    [Black Body.kicad_pcb, Black Body.kicad_sch]
2025-10-11 arc corners
    [Black Body Breakout Board.kicad_sch]
2025-10-11 connector update
    [Black Body Breakout Board.kicad_pcb, Black Body.kicad_pcb]
2025-10-11 resistors added
    [Black Body.kicad_sch]
2025-10-15 updated bb
    [Black Body.kicad_pcb, Black Body.kicad_sch]
2025-10-18 updated silk screen
    [Black Body.kicad_pcb]
2025-10-19 updated connectors
    [Black Body Breakout Board.kicad_pcb, Black Body Breakout Board.kicad_sch, Black Body.kicad_pcb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]
2025-10-19 fixed edge cuts BO
    [Black Body Breakout Board.kicad_pcb]
2025-10-19 gebers + BOM
    [Black Body Breakout Board-B_Cu.gbr, Black Body Breakout Board-B_Mask.gbr, Black Body Breakout Board-B_Paste.gbr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]
2025-10-19 3D models and gerber
    [1053131205.stp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]
2025-10-25 updated BOM
    [Black Body Breakout Board.kicad_pcb, Black Body.kicad_pcb]
2025-11-01 updated 3D model
    [Black Body.step]
2025-11-01 moved fuse
    [Black Body.kicad_pcb]
2025-11-04 updated step file
    [Black Body.step]
2026-01-17 better file system
    [1053131205.stp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]
2026-01-19 swap from mx150 to nanofit
    [Black Body.kicad_pcb, Black Body.kicad_sch, Black Body.step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]
2026-01-22 Updated KiCad Sharepoint
    [Black Body.kicad_pcb]
2026-01-22 repo fix
    [Black Body.step, Fuse.stp, Molex Nanofit 1x2 Connector.stp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]
2026-01-22 repo cleanup
    [Black Body Breakout Board-B_Cu.gbr, Black Body Breakout Board-B_Mask.gbr, Black Body Breakout Board-B_Paste.gbr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]
2026-01-22 fixed location of kicad sharepoint
    [PowerProtection.kicad_sch]
2026-01-23 new layout
    [Fuse 3658.STEP, Molex Nanofit 1x2 Connector.stp, Molex Nanofit 2x3 Connector.stp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]
2026-01-23 new layout 2.0
    [Black Body.kicad_pcb, Black Body.kicad_sch]
2026-01-23 cleaned up files for irrad board
    [Black Body Breakout Board-B_Cu.gbr, Black Body Breakout Board-B_Mask.gbr, Black Body Breakout Board-B_Paste.gbr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]
2026-01-24 Updated layout and 3D models
    [Black Body.kicad_pcb, Black Body.kicad_sch, Fuse 3658.STEP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]
2026-01-24 changed 3D models for breakout
    [Black Body Breakout Board.kicad_pcb, Black Body.kicad_pcb, Black Body.kicad_sch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]
2026-01-24 updated 3d models for aarav
    [Black Body Breakout Board.kicad_pcb, Black Body.kicad_pcb]
2026-01-24 updated irrad board layout + removed testpoints
    [Black Body.kicad_pcb]
2026-01-24 actual irrad board update
    [Black Body Breakout Board.kicad_pcb]
2026-01-24 updated irrad board
    [Black Body Breakout Board.kicad_pcb]
2026-01-25 updated 24V
    [Black Body.kicad_sch]
2026-01-25 updated 24Va
    [Black Body.kicad_pcb]
2026-01-28 added logic analyzer + LEDS
    [Black Body.kicad_pcb, Black Body.kicad_sch]
2026-01-28 updated fuse silkscreen, added open circuit to TC
    [Black Body Breakout Board.kicad_pcb, Black Body Breakout Board.kicad_sch, Black Body.kicad_pcb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]
2026-01-28 updated GND pads MCP600
    [Black Body.kicad_pcb]
2026-01-28 moved trace + cleaned up silkscreen
    [Black Body.kicad_pcb]
2026-01-29 new gerber files
    [Black Body-NPTH.drl, Black Body-PTH.drl]
2026-01-31 BOM update
    [Black Body Breakout Board-CuBottom.gbr, Black Body Breakout Board-CuTop.gbr, Black Body Breakout Board-EdgeCuts.gbr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]
2026-02-02 updated cap
    [Black Body Breakout Board.kicad_pcb, Black Body Breakout Board.kicad_sch, Black Body.kicad_pcb]
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2026-02-02 updated resistors 0805 to 0603
    [Black Body Breakout Board-CuBottom.gbr, Black Body Breakout Board-CuTop.gbr, Black Body Breakout Board-EdgeCuts.gbr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]
2026-02-02 updated ferrite bead values
    [Black Body-CuBottom.gbr, Black Body-CuTop.gbr, Black Body-EdgeCuts.gbr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]
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
